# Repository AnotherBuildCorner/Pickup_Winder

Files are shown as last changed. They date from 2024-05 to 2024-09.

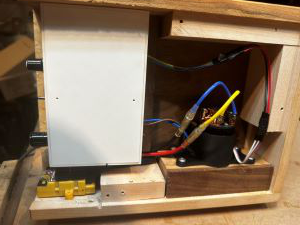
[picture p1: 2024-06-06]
Photos/IMG_5629.JPG

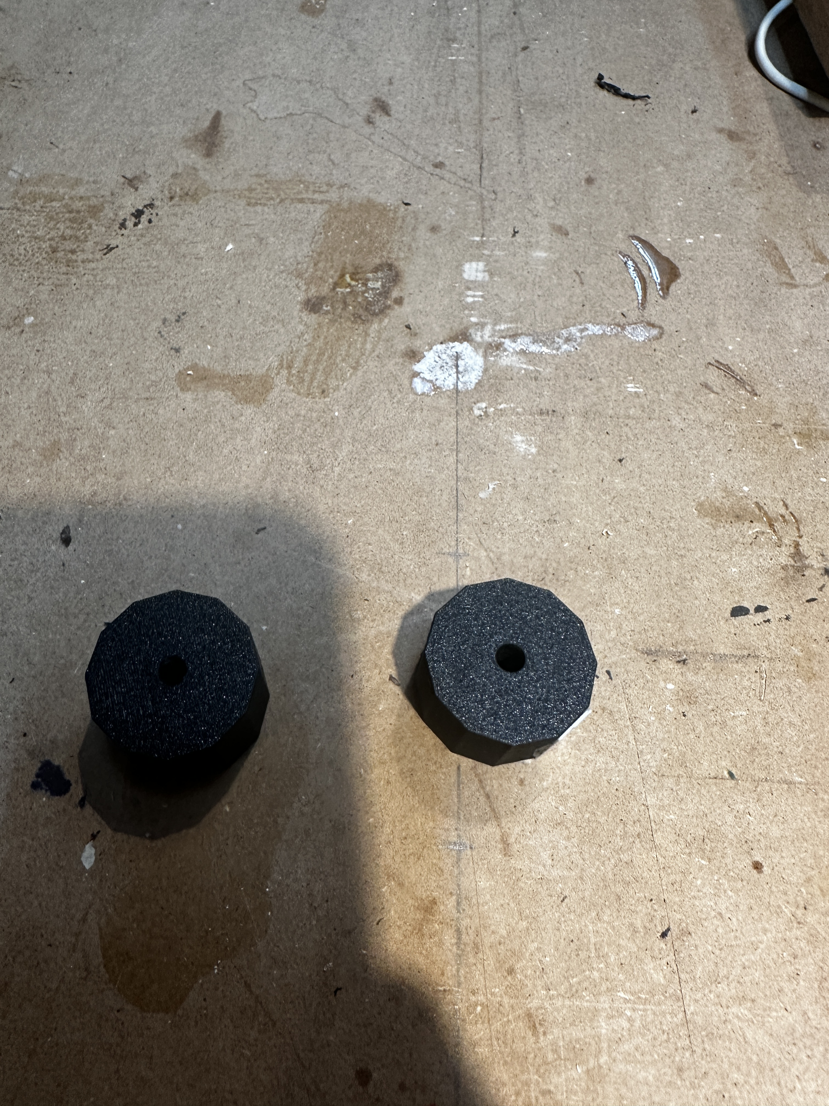
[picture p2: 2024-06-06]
Photos/IMG_5635.JPG

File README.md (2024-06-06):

# Pickup Coil Winder. V2
Tried looking for pickup winders on the internet, only to be blown away by the crazy price tags?

I bet you've tried the old school method of a Drill and your fingers, and I can also guess it didn't go well either.

Want the ability to wind a picckup bobbin, without breaking the bank, and without having to sit there with laser focus trying to keep that 42 gauge wire from breaking while the cat is in the way?

Then this design might just be what you need!

Based off of commonly available Hobby RC components, and an ESP32 microcontroller. With a small handful of 3D printed components added, this device can wind all your common guitar pickup bobbins with minimal user input.



### Overview:
At the heart of this design is a simple IO PCB with a 5V linear regulator, ESP32, and pin headers to connect other components


PCB Sch

And a 3D printed mechanics housing, integrating a 550 sized RC motor, 4:1 Pulley drive, 5mm bearing rod and bearings, encoder wheel, optical sensor, and optional Hall effect sensor
### (Full Drive Assembly model)
Drive Assembly v2

Assembly Video

https://github.com/AnotherBuildCorner/Pickup_Winder/assets/112969078/35dab373-d6de-44d6-9a98-b22964a5057d

### Motor and Esc

### Housing
Belt Drive v4
### Optical Encoder Wheel
Counter Wheel v3

### Large Pulley
V Pulley Large v2

### Small Pulley
V pulley small v3

### Optical Encoder location

### Hosuing with Hall Effect Sensor


### Annotated image:



On top Panel are three things: The OLED readout, the traverse servo and cradle, and the Wire tensioner/guide assembly.
The oled is a simple Adafruit 1306 OLED  128X64. in a custom holder
### OLED Holder
Oled Holder v4

The Traverse servo is a commonly available SG90 micro servo located in a 3d printed dovetail cradle with spring tension
### Traverse Servo Assembly
Servo Cradle v5

and the wire tensioner is a simple piece of plexiglass with a smooth hole in one end, with a pair of Cymbal felts tensioned by a bolt. The wire passes between the felts, and through a hole in the arm of the servo before being wound to the bobbin.

## Schematic


## Design Choices
### Why the RC components
Initially, back in V 0.5, a stepper motor driver was used instead of RC motors, which eliminates the need for other encoders.

However this proved unreliable in testing, as the motor torque was terrible, the drive would sometimes get confused and reverse, ruining the bobbin, and the stepper libraries caused the motor to ramp up and down in speed for the auto traverse.

At the time I also had some RC components laying about, and decided to try them as they were "free to me". And for a system to control the auto traverse, a micro servo was the simplest method available since all that's needed is a servo library and micro controller. 

### Belt Drive?
So i've tried direct drive, Gear drive, and belt drive.  They all have pros and cons.

For the direct drive. Motor selection becomes a primary concern. as 550 size RC motors are available in a multitude of torque and speed configurations defined by their turn count.

Problem is these motors are meant to run several thousand RPM. So the 1000 RPM needed is hard to control, and the speed jumps from too slow, to too fast easily. Plus the most commonly available motors don't have enough torque.

Also, if a hall effect sensor is added. the magnet is mounted to the drive flange, which causes instability at high speeds.

So, gear drive?
Two problems here. One is the geartrain to get a 4:1 reduction, as well as enough distance between motor and drive flange. is HUGE. 

Also, the noise was unbearable.

Belt drive on the other hand, has but one major downside over direct drive.  The additional bearings and shafts needed to support the drive flange add cost. 

5mm bore pulleys are easily obtainable and inexpensive. In fact, future versions may receive a CNC style timing belt drive.

### Why not an Arduino?
For a few reasons
One, Arduinos lack the general IO I wanted/needed to upgrade this system.  Version 1 was driven off of a Nano, and couldn't handle the inclusion of a rotary encoder

Two, I have a few ESP32's laying around from other projects, as well as experience using them

Three, ESP32's are Arduino code enabled. So no need to change code base

Four, ESP32's have integrated WiFi, Bluetooth, and Serial Coms. So if the desire should ever strike to create a webpage to control the winder, or maybe an app. The device is already ready to do so.

Five, ESP32's are pretty inexpensive. For the one I used, $10 for a 5MHz clock, around 20 available GPIO, and the communications above? No Brainer in my book.

## Features:

At present the enabled features are:
- Serial communication readout
- Multi screen OLED readout, including estimted DC resistance, wire length usage, and RPM
- Auto Traverse with multiple winding patterns available
- Variable speed and direction control with Auto Stop
- Multiple parameter adjustment, including:
  + Bobbin Size
  + Wire Gauge
  + Insulation Thickness
  + Winding Pattern
  + Faceplate Offset
  + Wind Count
  + Under/Overwind
  + Error margin
- Presets enabled via code edit
- Manual adjustment of winding via joystick control
- 
In the future a set of coded presets will be included and enabled via the Encoder knob and OLED. With the ability to adjust parameters after a preset is selected. This will completely untether the unit from a computer for general usage.

## Parts list
Note, some of these parts come in multiple quantites, prices reflect a Price Per in most cases
- 550 Motor and ESC, $30
- ESP32 Devkit-C V4, $10
- SG90 Micro Servo, $2.50
- Support Bearings, $2
- Drive Shaft, $2
- PCB, $8 for 5, with S&H included (minimum order)
- Cymbal Felts, $4
- Optical Sensor, $1
- Potentiometer, $1
- OLED, $5
- Rotary Encoder, $2
- Switch, $1
- Drive Belt material, $5
- Main Drive flange, $4

Links Will be added at a later date.  

## But what about those 3D parts
Critically, none of the 3D printed parts are a deal breaker for the design. The original V1 design (located below) used a plexiglass mount plate and no 3D printed parts.

The belt drive tower can easily be fashioned from a pair of plates, perhaps even wood. So long as the motor can be mounted to it via the faceplate screws, and the bearings fit with enough space for the encoder wheel, the rest is optional. 

The encoder wheel could be simply made with a block of material with a hole through the center, colored white on one side, and black on the other.

the servo cradle is a nice but not required extra. The original was held down by a plate secured with two screws (see V1 below)

The control box isn't required, just makes things a little nicer to look at. A simple piece of thin stock with holes cut in for the power jack, knobs, and switch is all that's needed.

## Some parts iterations.

### Previous version, and Gear drive towers



### Changes to pulleys 



### Servo cradle designs



## Original V1 design





The original design utilized an Arduino Nano microcontroller, with a direct drive motor, and custom infared light gate. With a circuit board built on a solderable breadboard. This functioned as an excelent prototype but had a few key problems I wanted to update.

First and foremost, direct drive has it's downsides. While being the quietest operation, it requires specific motor selection to achieve, as 550 size RC motors are classed by turn count, with 12T being a low torque high speed, and up to 80T being high torque Low speed.  Problem is 12T models are the most commonly available, and the speed controller can't control them effectively at the 1000 RPM range, and the available torque is borderline too low to overcome the wire tension.

Additionally, the direct drive requires adding the magnet to the flywheel for the hall sensor. This causes vibrations near the top speed.
Lastly, the Nano lacked the complete GPIO desired to run an OLED, encoder, servo, potentiometer, switch, and extras.
With the lack of an OLED and encoder, the system was permanently tethered to a computer for serial programming and monitoring.

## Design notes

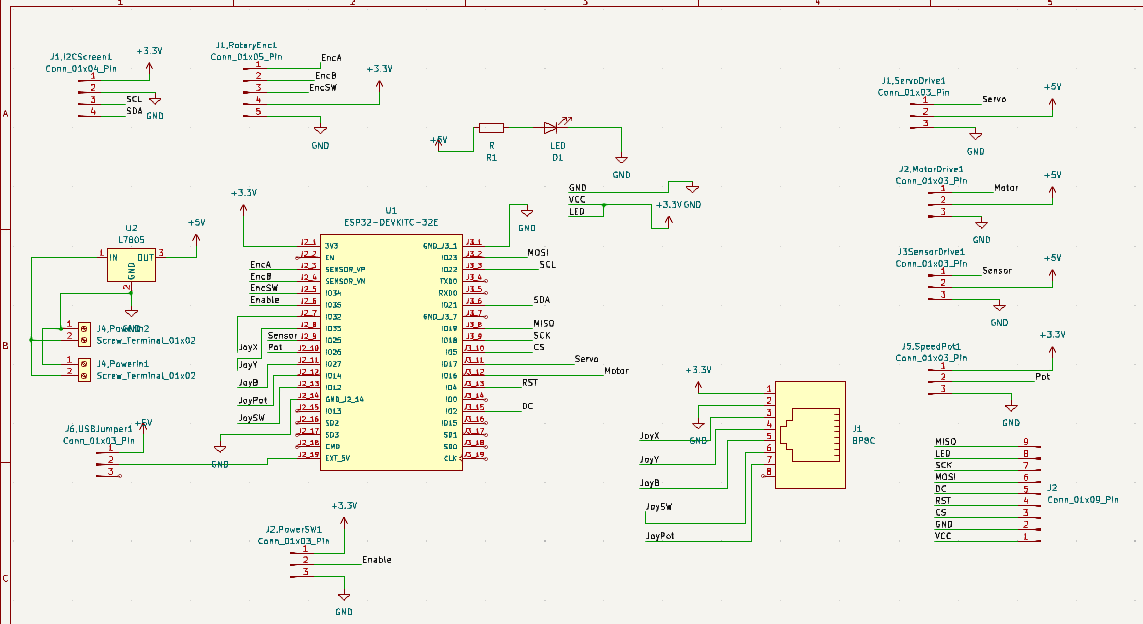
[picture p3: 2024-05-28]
Code/WinderPinout.png

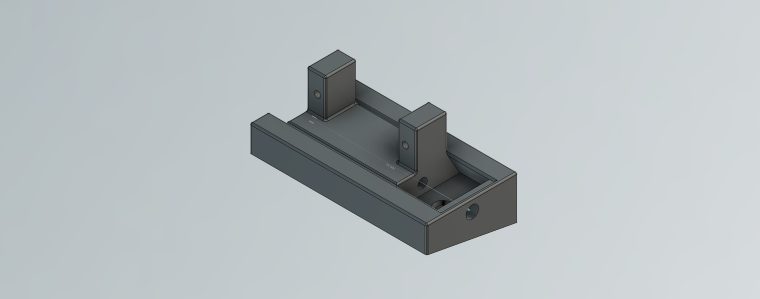
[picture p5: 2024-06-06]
Photos/Servo Cradle v5.png

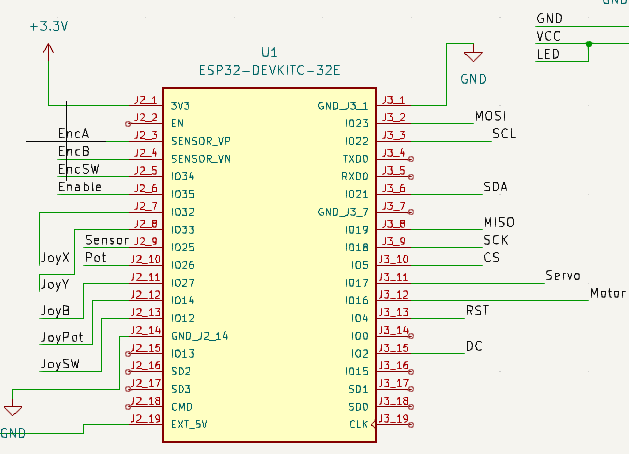
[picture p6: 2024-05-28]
Photos/Screenshot 2024-05-23 172855.png

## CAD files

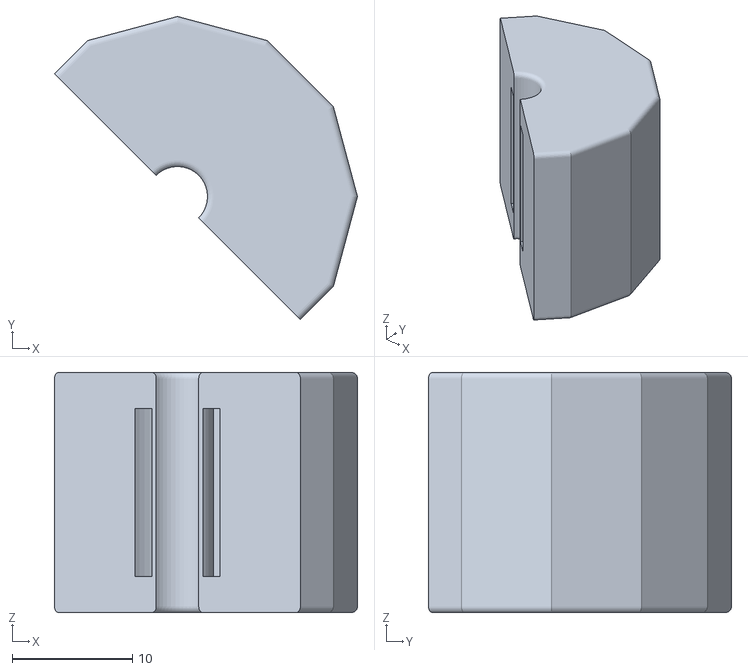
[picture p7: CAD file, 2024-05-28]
3D Meshes/Counter Bottom.stl
25.2 x 25.2 x 20.0

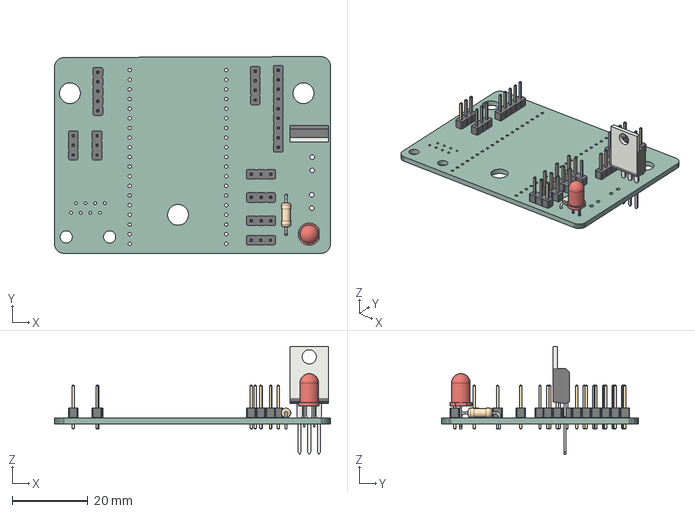
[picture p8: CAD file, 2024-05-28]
PCB/Winder_V1.step
72.6 x 51.8 x 28.5 mm
Winder_V1 PCB

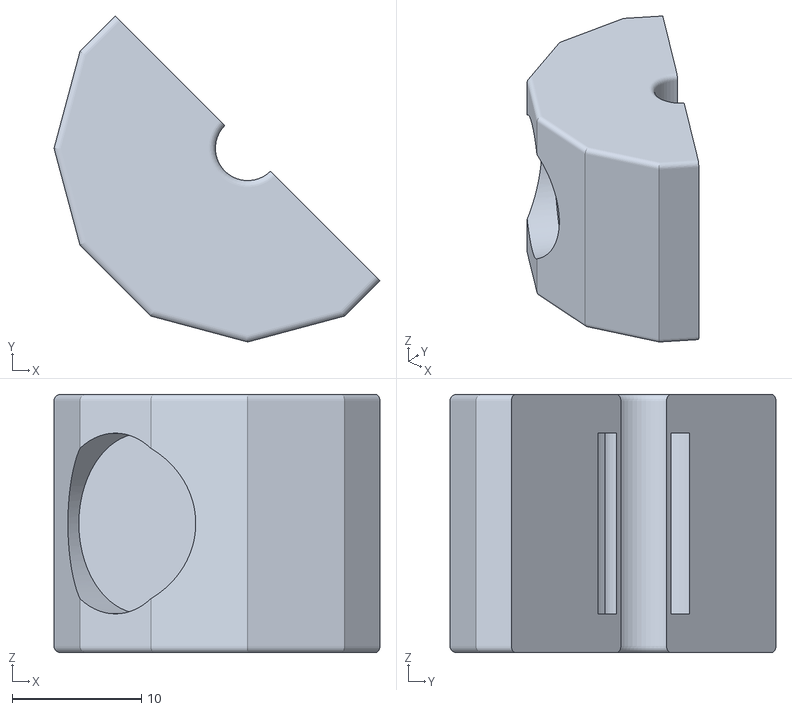
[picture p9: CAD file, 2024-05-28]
3D Meshes/Counter Top.stl
25.2 x 25.2 x 20.0

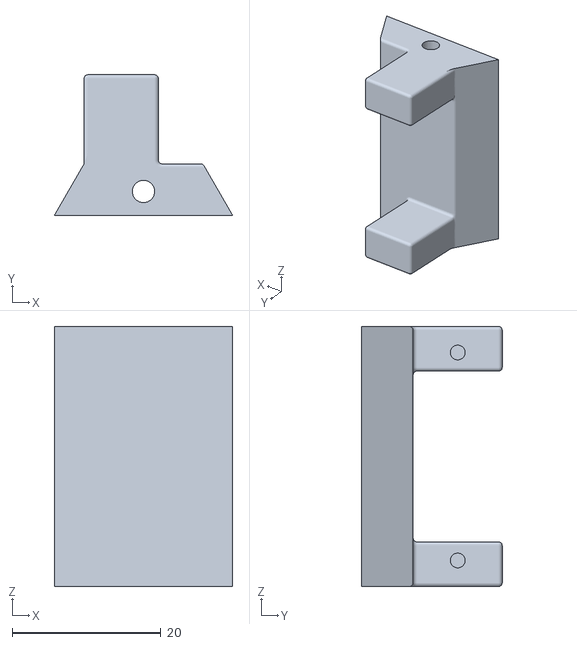
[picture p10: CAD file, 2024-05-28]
3D Meshes/Cradle.stl
24.0 x 18.9 x 35.0

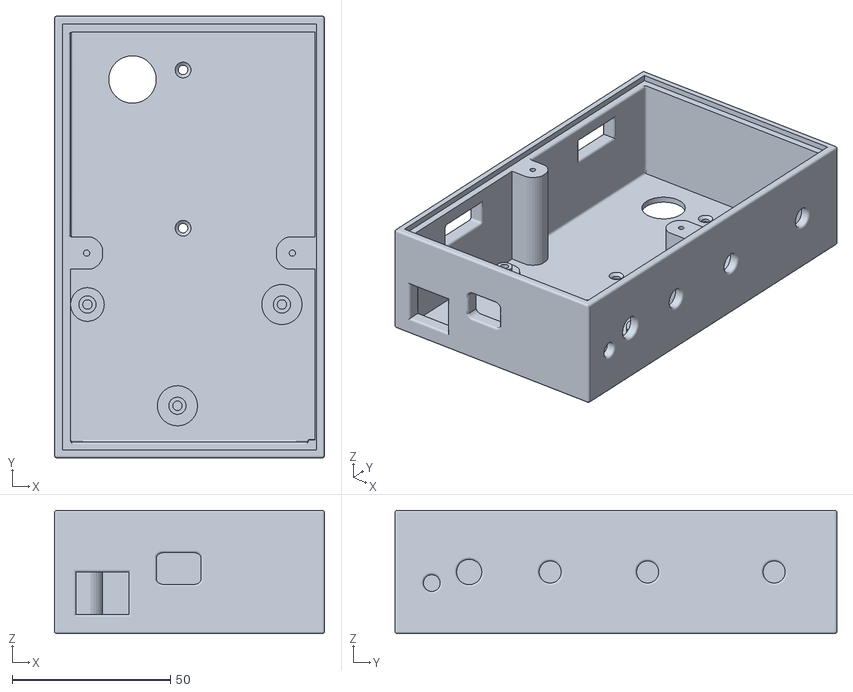
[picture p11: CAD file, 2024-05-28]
3D Meshes/Control Box.stl
85.3 x 139.7 x 39.0

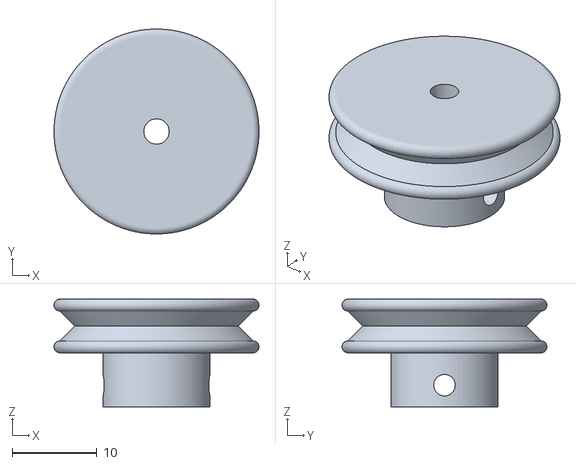
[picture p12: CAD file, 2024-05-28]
3D Meshes/V pulley small v3.stl
24.2 x 24.2 x 12.7

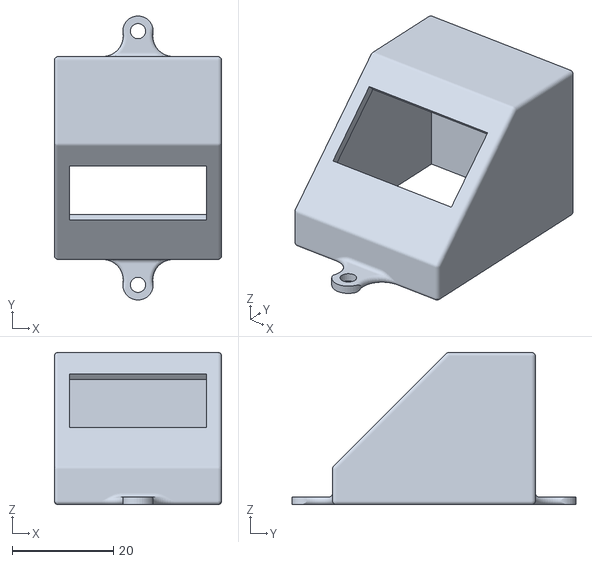
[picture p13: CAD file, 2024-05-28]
3D Meshes/Oled Holder v4.stl
33.0 x 56.0 x 30.0

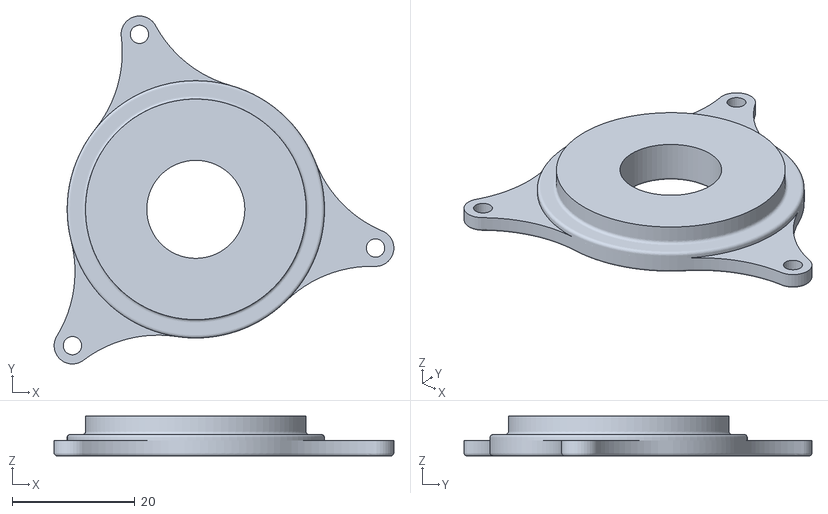
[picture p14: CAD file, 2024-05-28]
3D Meshes/Bearing Flange v1.stl
55.5 x 56.8 x 6.50

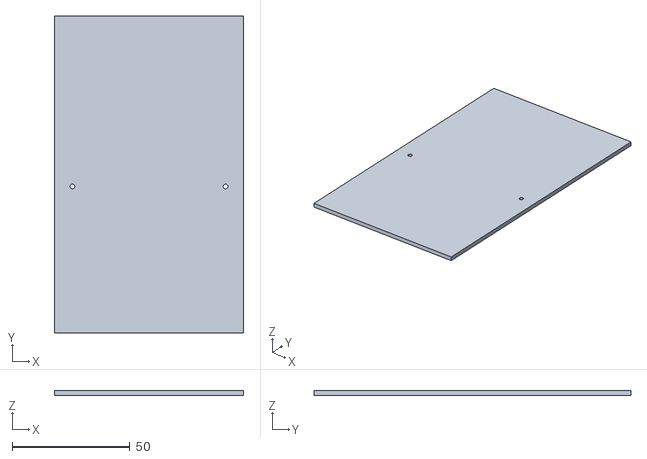
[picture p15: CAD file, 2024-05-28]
3D Meshes/Control Box Lid.stl
80.3 x 134.6 x 2.00

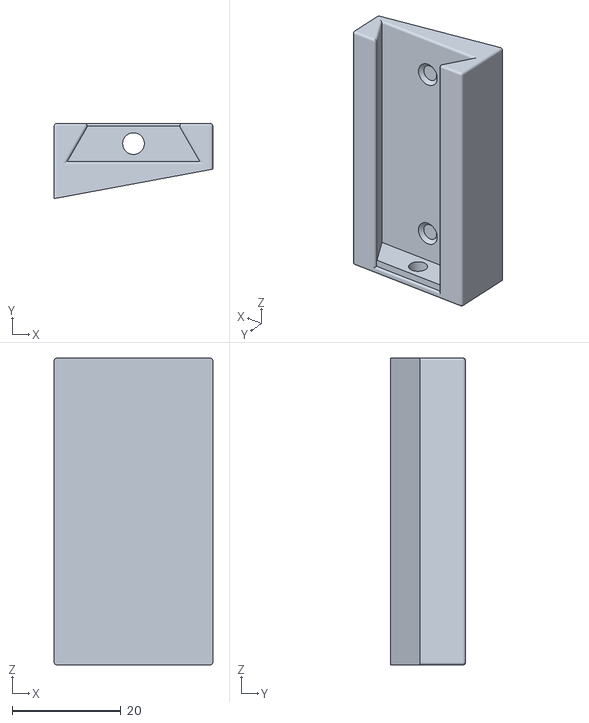
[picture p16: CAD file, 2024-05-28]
3D Meshes/Slide.stl
29.2 x 13.9 x 56.5

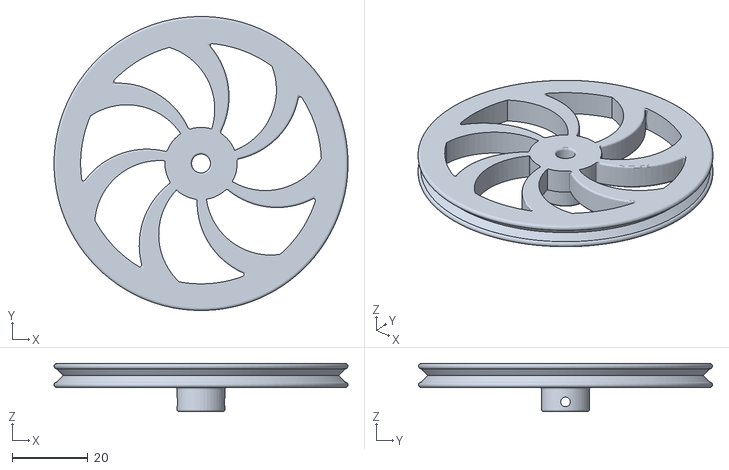
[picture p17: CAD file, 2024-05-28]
3D Meshes/V Pulley Large v2.stl
77.5 x 77.5 x 12.7

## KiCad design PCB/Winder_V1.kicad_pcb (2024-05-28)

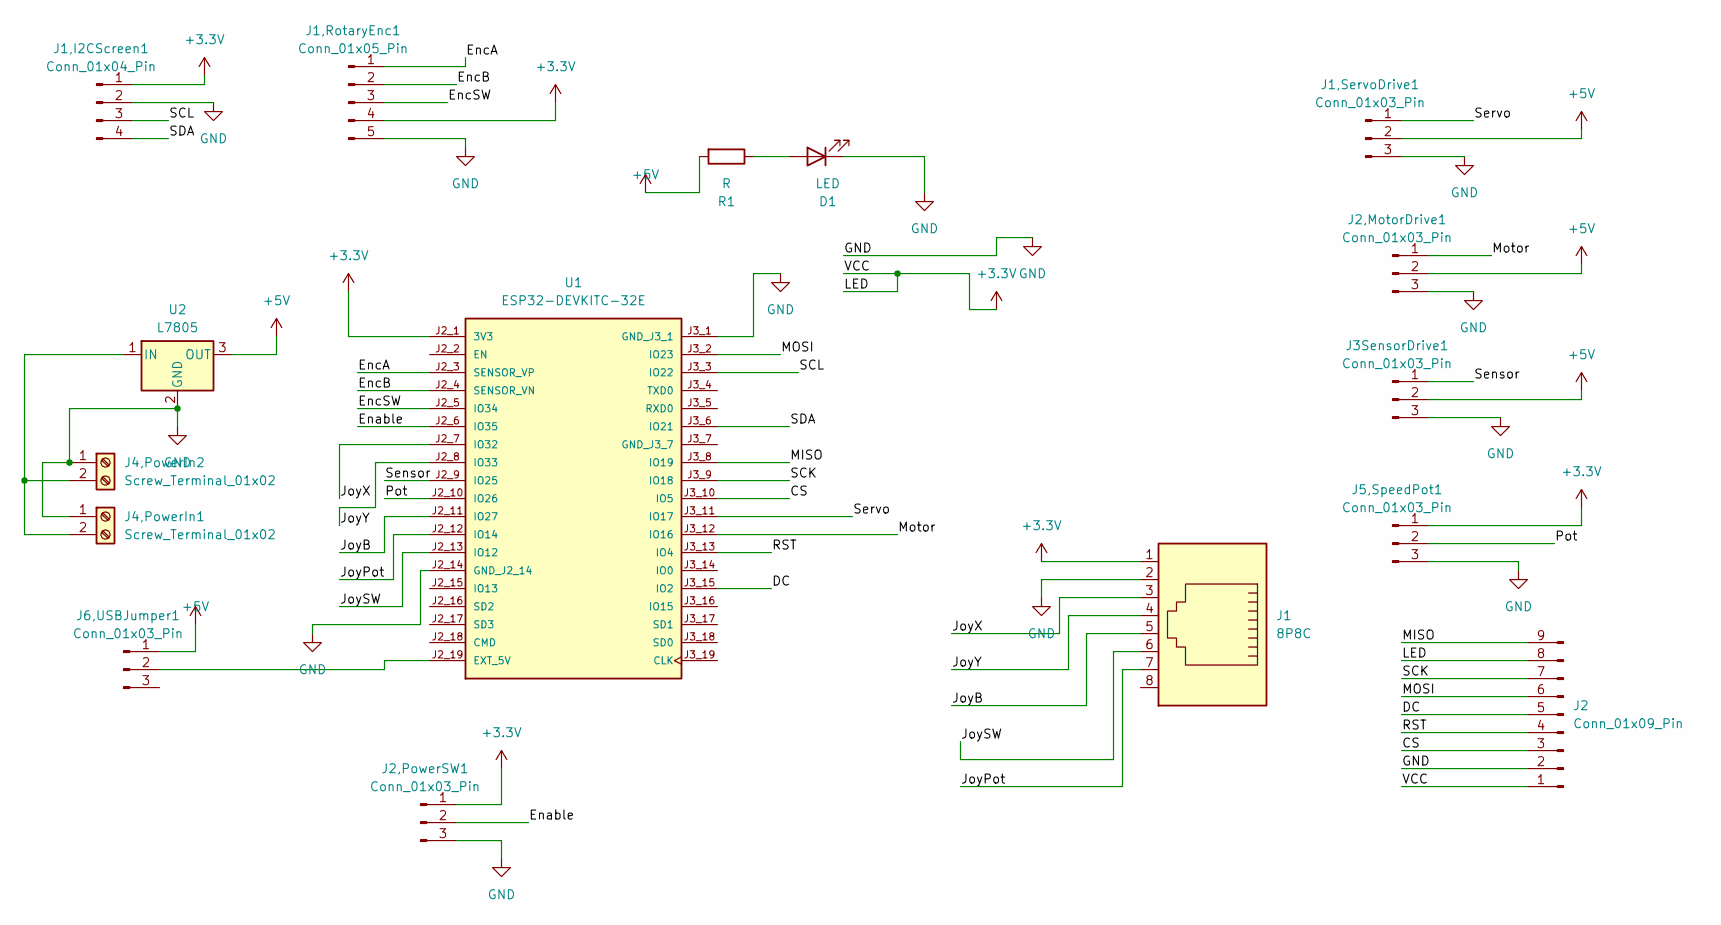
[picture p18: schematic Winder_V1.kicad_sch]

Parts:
D1: LED; LED_D5.0mm
J1: 8P8C; RJ45_Amphenol_54602-x08_Horizontal
J1,I2CScreen1: Conn_01x04_Pin; PinHeader_1x04_P2.54mm_Vertical
J1,RotaryEnc1: Conn_01x05_Pin; PinHeader_1x05_P2.54mm_Vertical
J1,ServoDrive1, J2,MotorDrive1, J2,PowerSW1, J3SensorDrive1, J5,SpeedPot1, J6,USBJumper1: Conn_01x03_Pin; PinHeader_1x03_P2.54mm_Vertical
J2: Conn_01x09_Pin; PinHeader_1x09_P2.54mm_Vertical
J4,PowerIn1, J4,PowerIn2: Screw_Terminal_01x02; TerminalBlock_4Ucon_1x02_P3.50mm_Horizontal
R1: R; R_Axial_DIN0207_L6.3mm_D2.5mm_P10.16mm_Horizontal
U1: ESP32-DEVKITC-32E; MODULE_ESP32-DEVKITC-32E; PARTREV 1.4
U2: L7805; TO-220-3_Vertical

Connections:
+3.3V: J1.1, J1,I2CScreen1.1, J1,RotaryEnc1.4, J2.1, J2.8, J2,PowerSW1.1, J5,SpeedPot1.1, U1.J2_1 (3V3)
+5V: J1,ServoDrive1.2, J2,MotorDrive1.2, J3SensorDrive1.2, J6,USBJumper1.1, R1.2, U2.3 (OUT)
/CS: J2.3, U1.J3_10 (IO5)
/DC: J2.5, U1.J3_15 (IO2)
/Enable: J2,PowerSW1.2, U1.J2_6 (IO35)
/EncA: J1,RotaryEnc1.1, U1.J2_3 (SENSOR_VP)
/EncB: J1,RotaryEnc1.2, U1.J2_4 (SENSOR_VN)
/EncSW: J1,RotaryEnc1.3, U1.J2_5 (IO34)
/JoyB: J1.5, U1.J2_11 (IO27)
/JoyPot: J1.7, U1.J2_12 (IO14)
/JoySW: J1.6, U1.J2_13 (IO12)
/JoyX: J1.3, U1.J2_7 (IO32)
/JoyY: J1.4, U1.J2_8 (IO33)
/MISO: J2.9, U1.J3_8 (IO19)
/MOSI: J2.6, U1.J3_2 (IO23)
/Motor: J2,MotorDrive1.1, U1.J3_12 (IO16)
/Pot: J5,SpeedPot1.2, U1.J2_10 (IO26)
/RST: J2.4, U1.J3_13 (IO4)
/SCK: J2.7, U1.J3_9 (IO18)
/SCL: J1,I2CScreen1.3, U1.J3_3 (IO22)
/SDA: J1,I2CScreen1.4, U1.J3_6 (IO21)
/Sensor: J3SensorDrive1.1, U1.J2_9 (IO25)
/Servo: J1,ServoDrive1.1, U1.J3_11 (IO17)
GND: D1.1 (K), J1.2, J1,I2CScreen1.2, J1,RotaryEnc1.5, J1,ServoDrive1.3, J2.2, J2,MotorDrive1.3, J2,PowerSW1.3, J3SensorDrive1.3, J4,PowerIn1.1, J4,PowerIn2.1, J5,SpeedPot1.3, U1.J2_14 (GND_J2_14), U1.J3_1 (GND_J3_1), U2.2 (GND)
unnamed: D1.2 (A), R1.1
unnamed: J4,PowerIn1.2, J4,PowerIn2.2, U2.1 (IN)
unnamed: J6,USBJumper1.2, U1.J2_19 (EXT_5V)

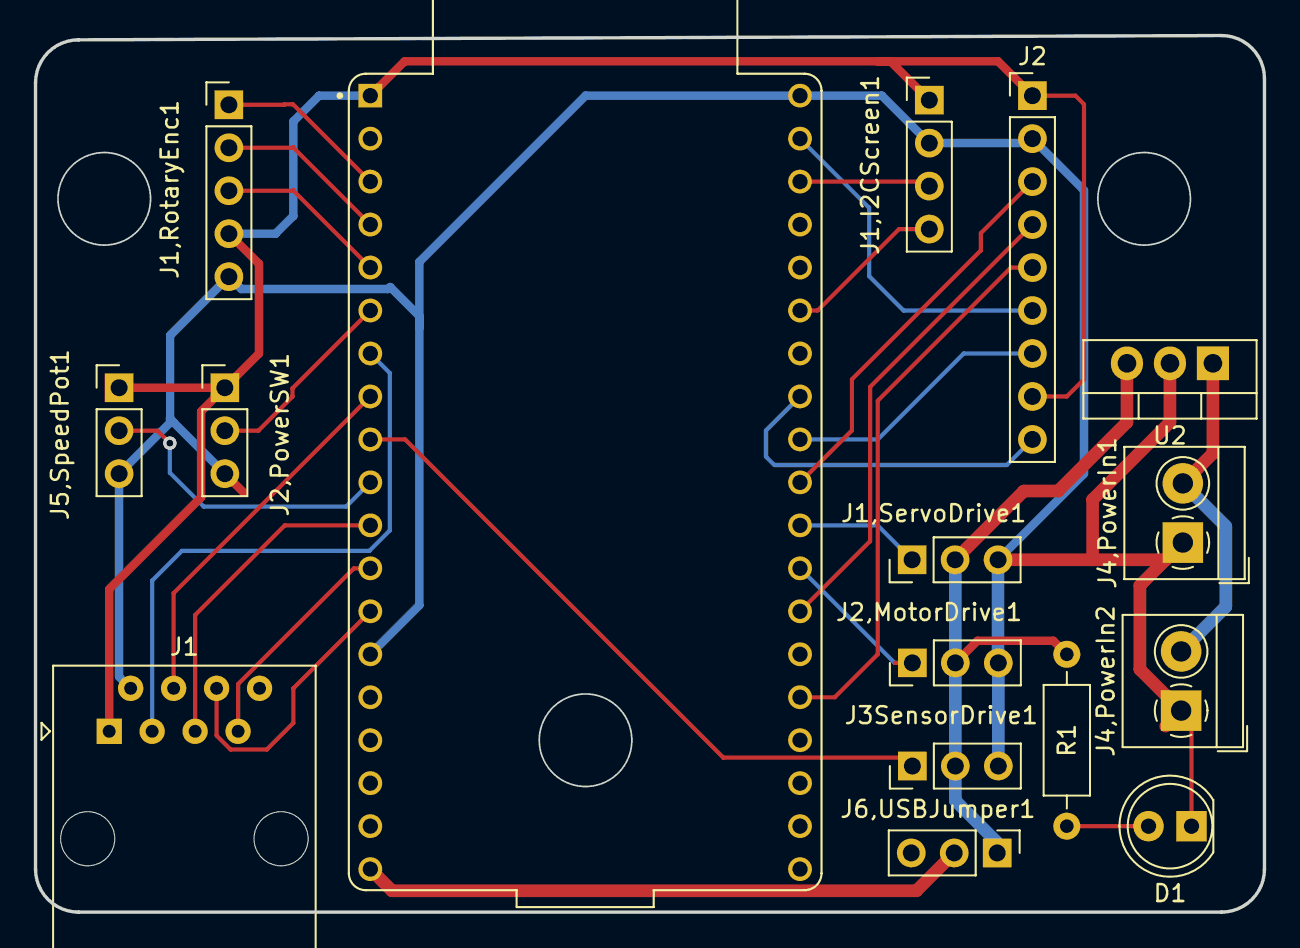
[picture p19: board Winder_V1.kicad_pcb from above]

Board: 2 copper layers, 72.6 x 51.8 mm, 16 parts (0 on the bottom side), 27 nets.

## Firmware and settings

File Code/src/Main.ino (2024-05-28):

#include <Screen.ino>

#define revdiv 2

// --------------------Startup code--------------------
void setup()
{  
   display.begin(SSD1306_SWITCHCAPVCC, OLED_ADDR);
   Serial.begin(9600);

             // set up Serial library at 9600 bps
  PinDeclare();
  Calculate_len();
   //Presets();
   
 //analogWrite(GateLED,GateLEDPwr);
 ESC.attach(ESCPin);
 servo.attach(ServoPin);  
 TestScreen();  
 startup_disp(); 
 delay(1000);
}

//--------------------- Main code -------------------------------
void loop(){
static bool disable_flag = false;
int t1 = millis();
int sw;
static int screen = 1;
static int t2 = 0;
if(disable_flag == false){


GateCount();
SpeedControl();
RangeTest();
StatusV2();

sw = Enc_Sw(t1);

screen = RunScreenCtrl(screen,sw,3);
if(t1 - refresh > t2){
  t2 = t1;
  if (Go == true){
  //rev_count += 50;
  }
Serial.println(GateRead);
RunScreen(Go,rev_count,t1,screen);
}


if (rev_count < winds){  
if(rev_count < winds-Spool){
  Go = digitalRead(SwitchPin);}


if(Go == true && HandWind == false){
//current_angle = ServoDir(current_angle,dir,steps);
dir = Flip(current_angle);  

          
}}}

if(rev_count >= winds-Spool){
Go = false;        
}


if(rev_count >= winds){


  if(disable_flag == false){
    Go = false;
   disable_flag = true;
    Serial.println("Winding Finished");
    Serial.println(rev_count);
    Calculate_len();
    FinishScreen(rev_count,full_len,DC);
    delay(1000);

  }

  ExitCtrl(t1,t2);
  

   
    
    
    }}
    

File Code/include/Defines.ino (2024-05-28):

#include <Arduino.h>
#include <ESP32Servo.h>

#include <Adafruit_SSD1306.h>
#include <Adafruit_I2CDevice.h>
#include <Wire.h>
#include <SPI.h>
// Need to update for the ESP32 pinouts
#define GatePin 25

#define GateLED 9
#define GateLEDPwr 255
#define GateMin 0
#define GateMax 100

#define PotPin 26
#define Potmin 4095
#define Potmax 0

#define SwitchPin 35
#define ESCPin 16
#define ServoPin 17
#define CWMaxSpeed_Def 55 
#define CCWMaxSpeed_def 135
#define Stop 95
#define Spool  2
#define SpoolRPM 200

#define EncoderA 36 // Sensor VP  
#define EncoderB 39 // Sensor VN
#define EncoderSW 34

#define JoyX 32
#define JoyY 33
#define JoyB 27
#define JoyPot 14
#define JoySW 12

#define MOSI 23
#define MISO 

#define refresh 500
Servo ESC;
Servo servo;


void PinDeclare(){
pinMode(SwitchPin,INPUT_PULLUP);
pinMode(EncoderSW,INPUT_PULLUP);
pinMode(PotPin,INPUT);
pinMode(JoyX,INPUT);
pinMode(JoyY,INPUT);

  
}
//ccw vs cw.  6000 = 7.7k DCR, CW. 4.6 CCW 6000 vs 8000 makes same coil size

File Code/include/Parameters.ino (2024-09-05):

// ----------------------- Servo Parameters----------------------
int wind_count = 8750;
float arm_length = 13;//arm length from servo center in mm.  19 standard
int underwind = 0; //% underwind  set overwind to 0
int overwind = 0; //% overwind, set underwind to 0
int spin_dir = -1; // set to -1 for Counter Clockwise, and 1 for Clockwise.
float faceplateOffset =0; // distance off of the faceplate to the inside of the bobbin, good for thicker flatwork.
float error_margin = 5; // Percent of bobbin width to remove for accident prevention.

//-------------------------- Bobbin Parameters-----------------------


float bobbin_width = 11; //Width in Millimeters gap between two faces for winds.
float bobbin_length = 57; // Length of bobbin in mm. just for estimating wire usage.
float bobbin_height = 5; // Width across bobbin in mm. just for esitmating wire usage,

//------------------- Extra parameters---------------

int scatterwind = 4; // Set to 1 for random per Layer, 2 for Pattern per step,.
bool HandWind = false; // Shuts down the servo, for hand winding.  recode for manual servo sweep maybe?

int servoZeroInt = 35; // used to set the minimum point for the servo arm, closest to the plate.
float wire_gauge = .0030; //Wire gauge 0.0030 for heavy  0.0025 standard
float wire_unit = 25.4;  //(set to 25.4 for inches, 1 for mm)
int ScatterMin = 1; // scatterwind steps. for the randomizer,
int ScatterMax = 10;
int Pattern [] = {1,3,7,3,2,1,5,2,1,2};
int* ScatterPattern = Pattern;
int Patternlength = 10;
int patternplace = 1;
